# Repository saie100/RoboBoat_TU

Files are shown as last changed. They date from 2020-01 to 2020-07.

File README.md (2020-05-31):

# Temple University RoboBoat - Senior Design 2020 #



## Table of Contents ##

1. ### [ROS Packages & Implementation](/ROS_Packages#ros-packages) ###
    1. [Status Indicator Light & Autonomous Mode Select](ROS_Packages/roboboat_control_status)
    1. [Rosserial - multiple serial nodes](ROS_Packages/roboboat_rosserial)
    
1. ### [Arduino Code](Arduino_Files/) ###
    
1. ### [Shell Scripts](Shell_Scripts/) ### 
    1. [General Use of the Shell Scripts](/Shell_Scripts#general-use-of-the-shell-scripts)
    1. [Starting and stopping the boat's software](/Shell_Scripts#starting-and-stopping-the-boats-software)
    1. [Starting and stopping the boat's software for debugging](/Shell_Scripts#starting-and-stopping-the-boats-software-for-debugging)
    1. [Creating rosbag recordings](/Shell_Scripts#creating-rosbag-recordings)

1. ### [The Boat's Control Interface (Website)](Boat_Website/) ### 
    1. [HTML Code](Boat_Website/index.html)
    1. [Javascript Code](Boat_Website/src/)
    1. [CSS Styling](Boat_Website/main.css)
    
1. ### [The Computer Hardware](Computer_Hardware/) ### 

1. ### [Networking](Networking/) ###
    1. [IP Addresses for the Networking Devices](Networking#network-hardware-ips)
    1. [Reserved Device IP Addresses](Networking/README.md#reserved-device-ips)
    1. [Modifying the WDS Bridge](Networking/Modifying_WiFi_Bridge.md)
    1. [Backup & Restore the Network Equipment](Networking/RouterBackups/)
    1. [Connecting the Boat to the Internet](Networking/Connect_to_Internet.md)
    1. [Documentation from the Manufacturers](Networking/README.md#hardware-documentation)

1. ### [KiCad Circuit Schematics](KiCad_Schematics/) ###
    1. [Schematic PDF Files & Images](KiCad_Schematics/SchematicExports/)
    1. [Battery Monitoring System (KiCad Project)](KiCad_Schematics/BatteryMonitor)
    1. [Emergency Transmitter/Receiver & Status Indicator Light (KiCad Project)](KiCad_Schematics/EmergencySystem)
    1. [Power Distribution & Protection (KiCad Project)](KiCad_Schematics/PowerDistribution)
    1. [Teensy3.2 for Motor Control, GPS, and IMU (KiCad Project)](KiCad_Schematics/TeensySchematic)

1. ### [CAD Designs](CAD_Files/) ###
    1. [Motor Mounts](CAD_Files/MotorMounts/)
    1. [Cable Cover](CAD_Files/CableCover/)
    1. [Teensy3.2 Enclosure](CAD_Files/TeensyEnclosure/)
    1. [LIDAR Enclosure](CAD_Files/LidarEnclosure/)
    1. [Other Parts](CAD_Files/Z-Other/)

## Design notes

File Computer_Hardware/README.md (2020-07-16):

# Computer Hardware #

## Configuration Guides ##

## [Raspberry Pi 4 Ubuntu Server - A Guide by James Chambers](https://jamesachambers.com/raspberry-pi-4-ubuntu-server-desktop-18-04-3-image-unofficial/) ##
This guide was used to install Ubuntu Server on the Raspberry Pi 4 so that ROS did not need to be compipled when installing.   

## [Develop on SSD - NVIDIA Jetson TX Dev Kits](https://youtu.be/ZpQgRdg8RmA) ##
The guide listed below was used to configure the TX2 to boot from an SSD. 

*Note: Only follow the guide up 4:57. Do not follow the steps after this time.*

## Creating/Restoring Backups Using a Linux Computer ##
### Creating a Backup ###
1. Connect the Micro SD card from the Raspberry Pi or the SSD from the TX2 to the computer where the backup will be made. 
1. Unmount the Micro SD card or the SSD from the OS - this can be done in the disk manager. 
1. Use the following command after substituting the path to the Micro SD card or the SSD and specifing a name for the compressed backup of the drive.
```
	sudo dd if=/dev/r[INSERT_DISK_HERE(disk2)] BS=32m | gzip > /[INSERT_PATH_AND_BACKUP_NAME_HERE].gz
```
### Restoring a Backup ###
1. To write the backup to a Micro SD card or SSD, first connect the drive to the computer and unmount the disk. 
1. Use the following command after substituting the name of the drive to be written to and the name of the backup file.  
```
	gzip -dc /[INSERT_PATH_AND_BACKUP_NAME_HERE].gz | sudo dd of=/dev/r[INSERT_DISK_HERE(disk3)] BS=32m
```

## [DOWNLOAD: Raspberry Pi 4B - Ubuntu Server Backup](https://drive.google.com/uc?export=download&confirm=n3Q3&id=1xh1nTMyLx9h_HU1v4K-zJbxssuq-ram7) ##
*Note: This backup must be restored to a Micro SD Card with a capacity greater than or equal to 64GB*

## [DOWNLOAD: Jetson TX2 - NVIDIA Jetpack Backup](https://drive.google.com/uc?id=1ChVVHlB_Lbe0hwe4Fh0JUX25fiE8jmSy&export=download) ##
*Note: This backup must be restored to an SSD with a capacity greater than or equal to 500GB*

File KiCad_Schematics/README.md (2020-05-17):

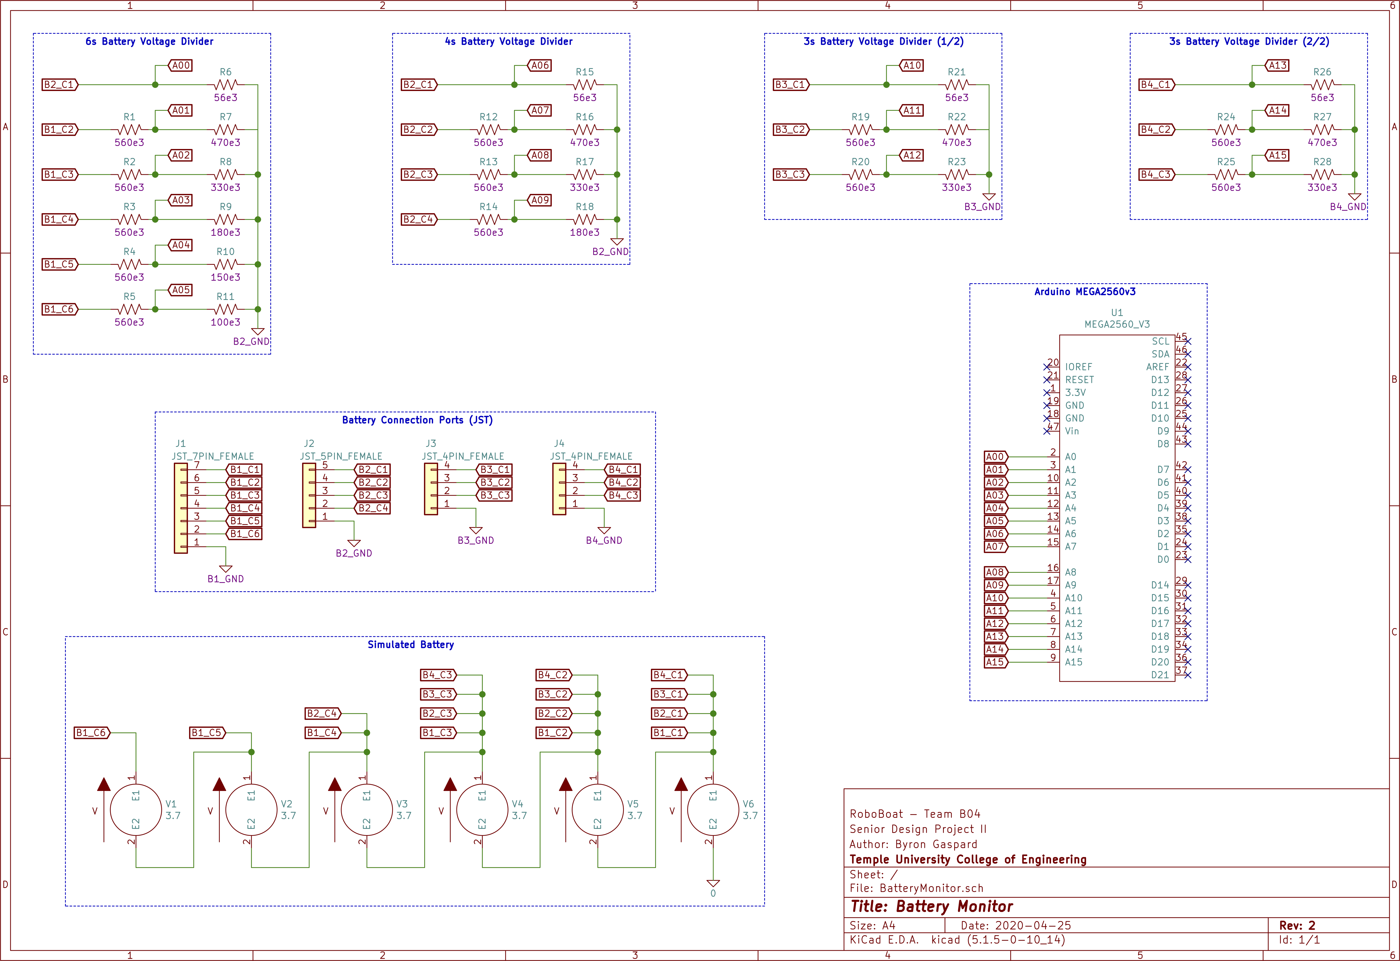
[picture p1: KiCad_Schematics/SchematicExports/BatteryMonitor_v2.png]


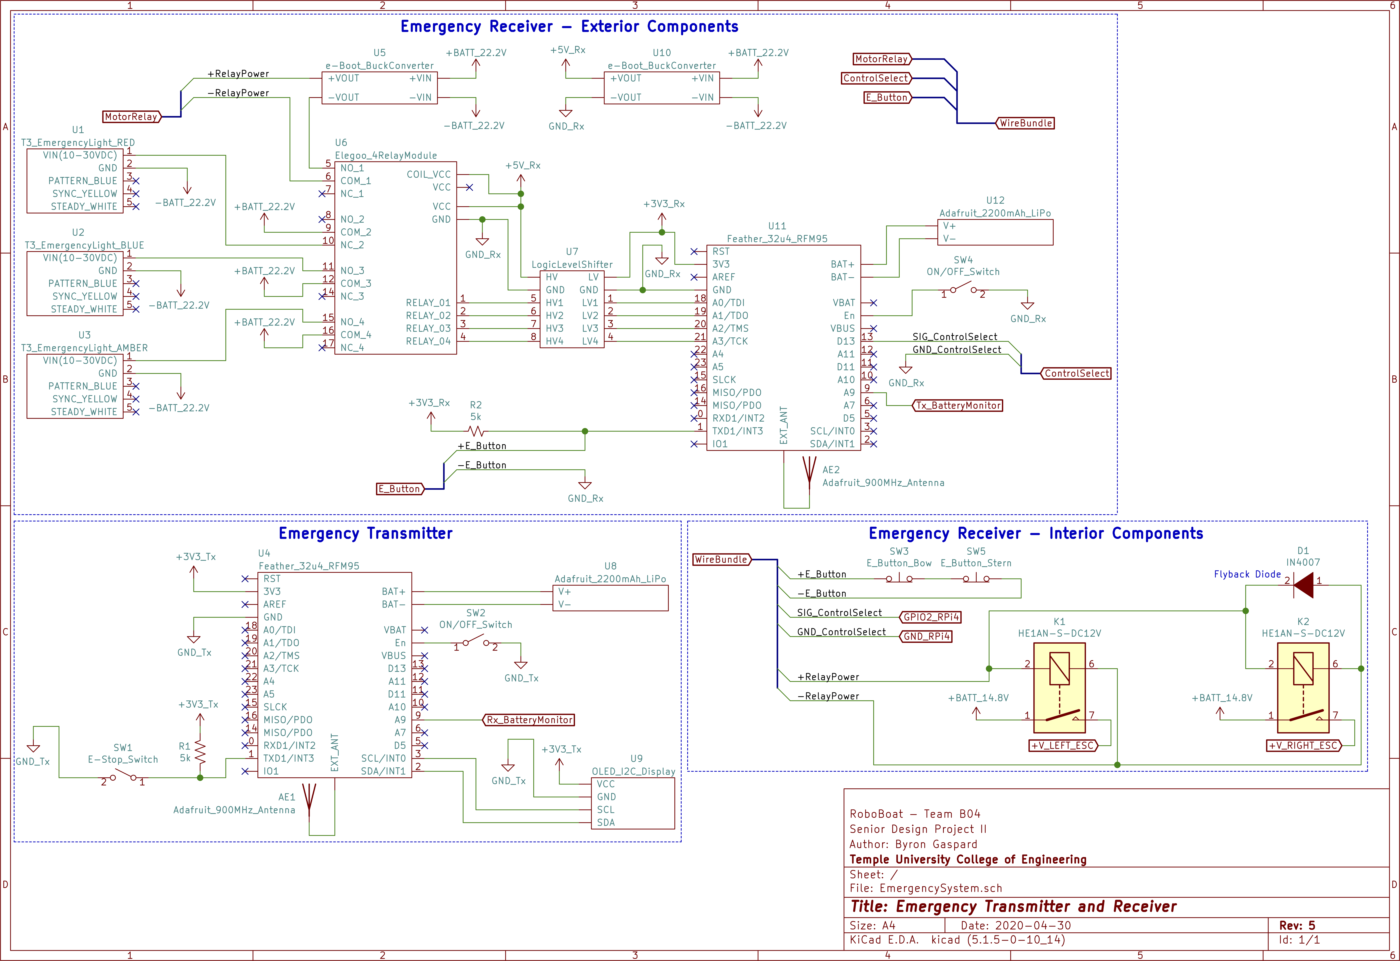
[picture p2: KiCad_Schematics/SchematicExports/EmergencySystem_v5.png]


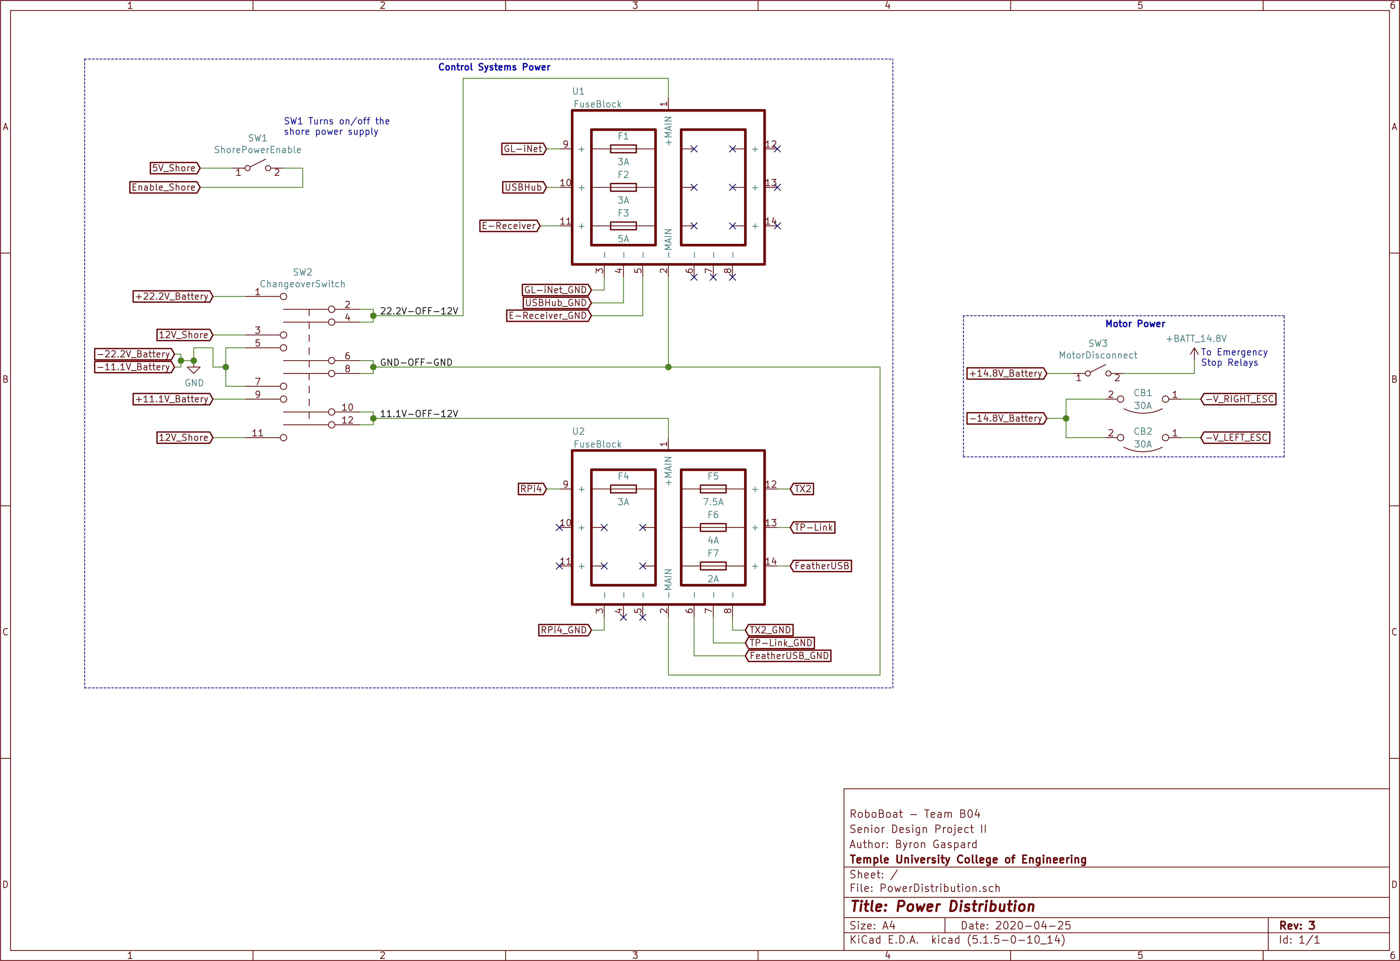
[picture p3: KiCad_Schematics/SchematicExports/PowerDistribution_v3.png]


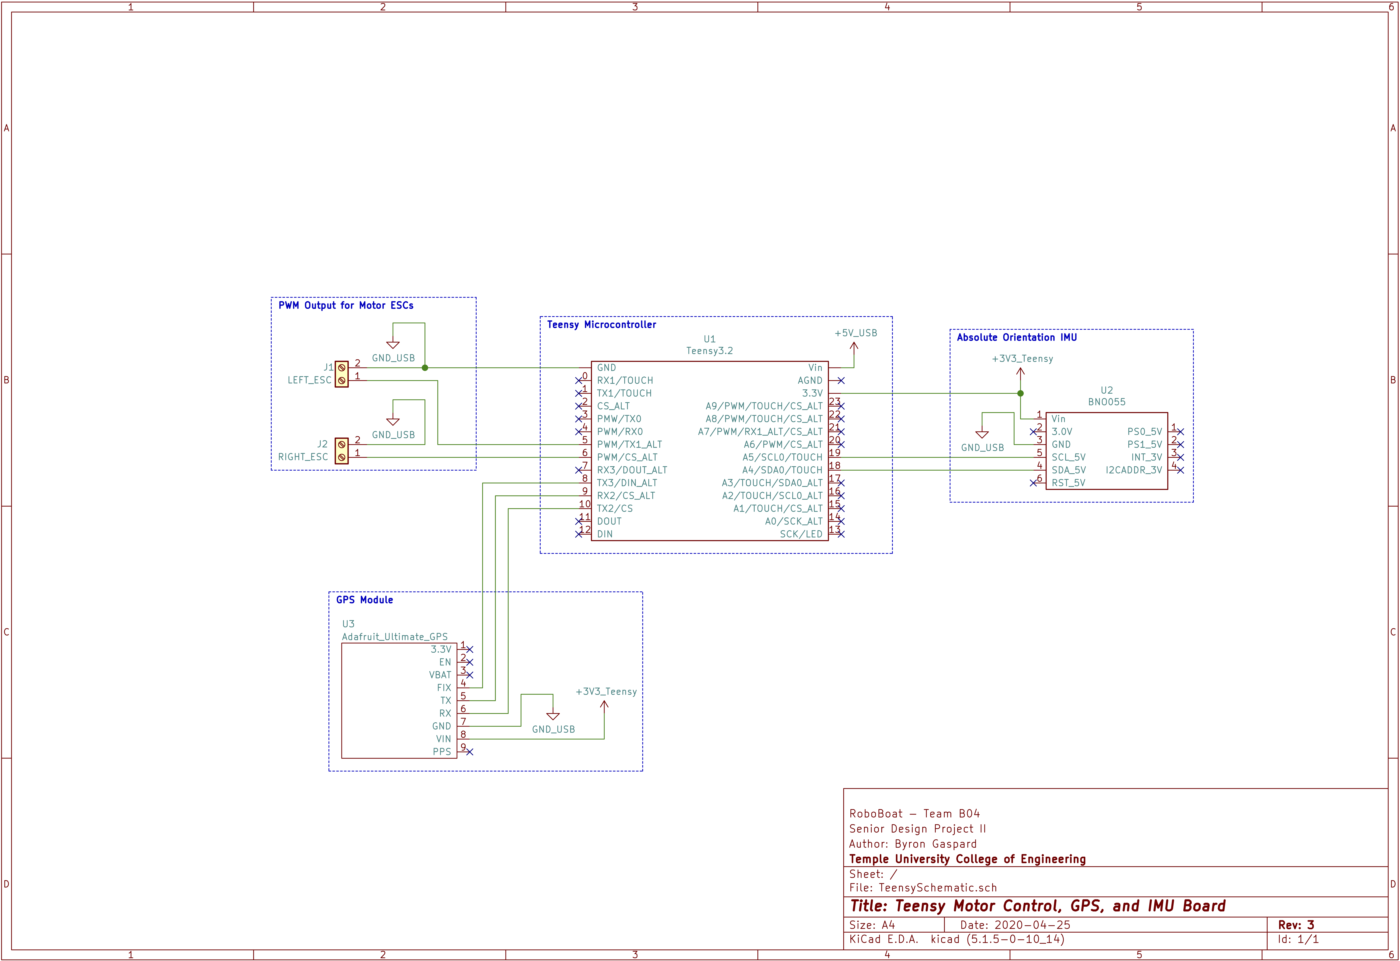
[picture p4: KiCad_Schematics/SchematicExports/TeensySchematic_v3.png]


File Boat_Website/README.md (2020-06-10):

# Overview of the Boat's Control Interface #

## JavaScript Libraries ##
1. [roslibjs](http://wiki.ros.org/roslibjs) - Allows ROS to be accessed and interacted with from a browser.
1. [Chart.js](https://www.chartjs.org/) - Provides JavaScript charting for displaying sensor data.
1. [Mapbox GL JS](https://docs.mapbox.com/mapbox-gl-js/api/) - Provides JavaScript map generation for displaying GPS sensor data recorded on the boat.
1. [xeogl](https://xeogl.org/) - A WebGL 3D visualization engine with support for displaying and animating 3D models.

---
## Custom JavaScript Code ##
1. [ros_setup.js](src/ros_setup.js)
1. [ros_handlers.js](src/ros_handlers.js)
1. [gamepad_control](src/gamepad_control.js)
1. [chart_create.js](src/chart_create.js)
1. [chart_update.js](src/chart_update.js)
1. [OrientationAnimation.js](src/OrientationAnimation.js)

--- 
## Controlling the boat from the website ##
The image at the bottom of this page shows the final version of the boat's website. 

The [Logitech F310 Controller](https://www.logitechg.com/en-us/products/gamepads/f310-gamepad.html) is used to manually drive the boat.

Steps to activate manual control:
1. Connect the Logitech F310 to the computer that is on the boat's website
1. Press any button on the controller - this will "wake up" the website and let it know that a controller is connected
1. Without pressing either of the joysticks, press the the "**Start**" button on the controller to zero the controller axis. 
1. The left and right motors on the boat can now be controlled independently using the left and right joystics on the F310. The axis can be re-zeroed at any point by pressing the "**Start**" button on the controller again.  



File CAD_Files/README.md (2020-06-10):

---

<p align="center">
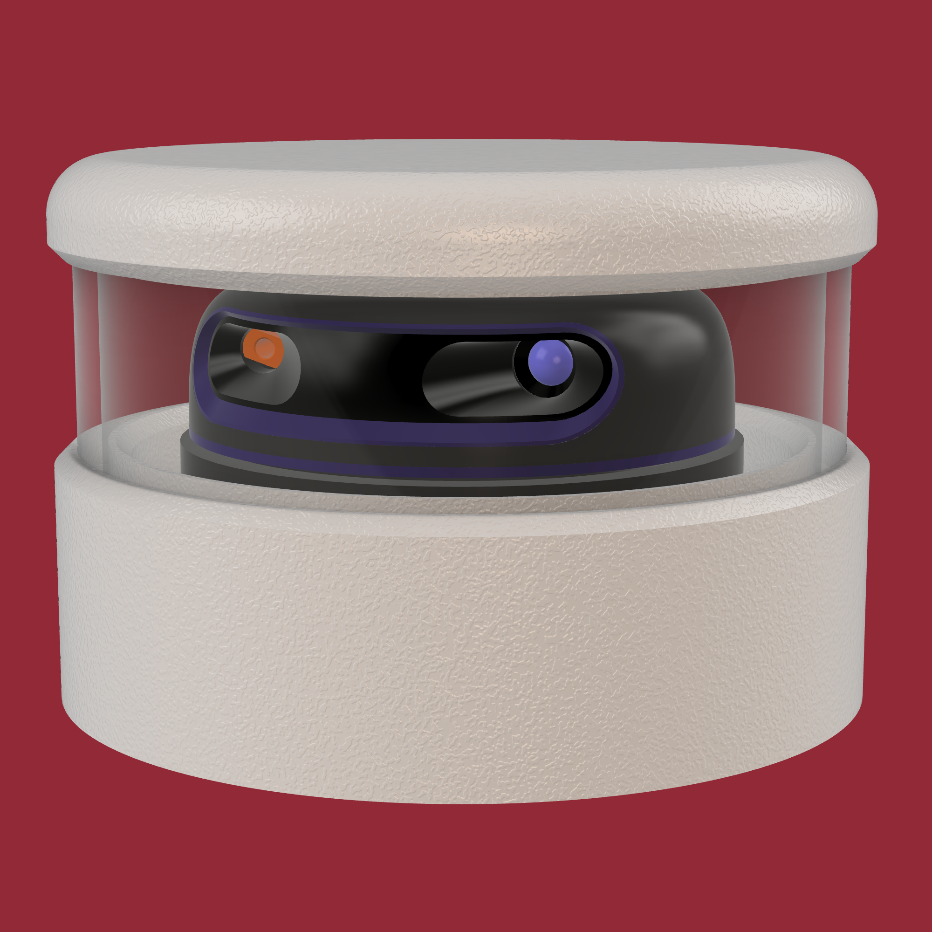
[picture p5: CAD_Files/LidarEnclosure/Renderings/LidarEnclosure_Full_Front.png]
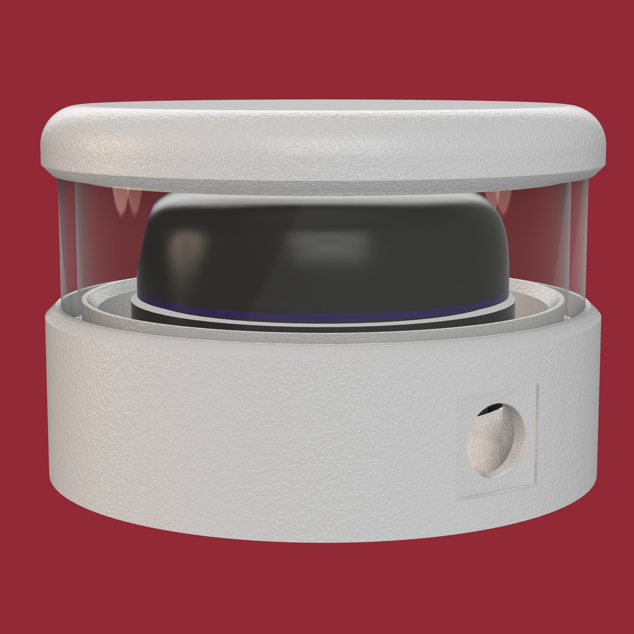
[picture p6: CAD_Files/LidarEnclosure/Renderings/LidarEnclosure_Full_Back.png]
   
</p>

---

<p align="center">
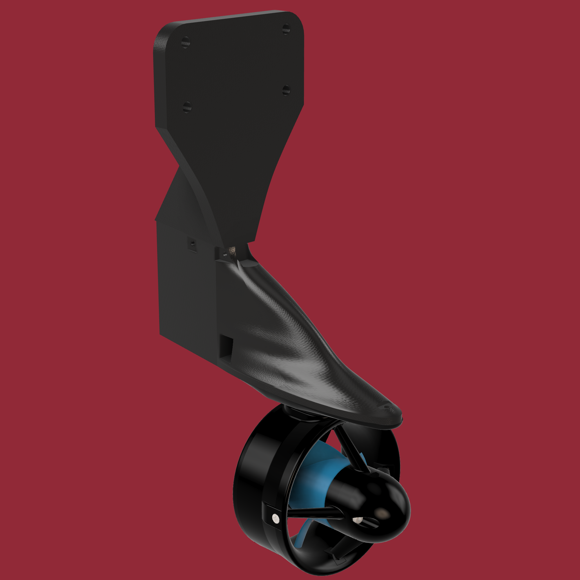
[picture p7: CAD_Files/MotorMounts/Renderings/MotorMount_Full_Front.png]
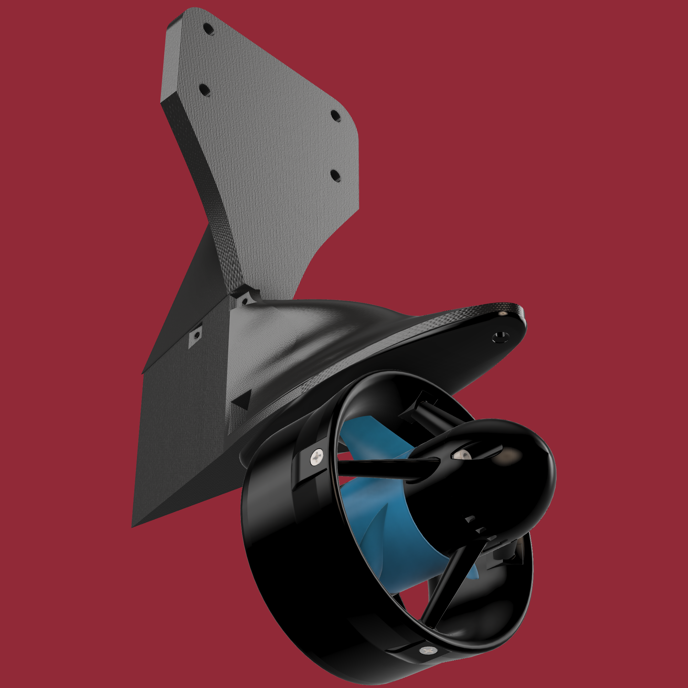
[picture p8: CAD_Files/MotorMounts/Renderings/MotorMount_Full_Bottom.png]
   
</p>

---

<p align="center">
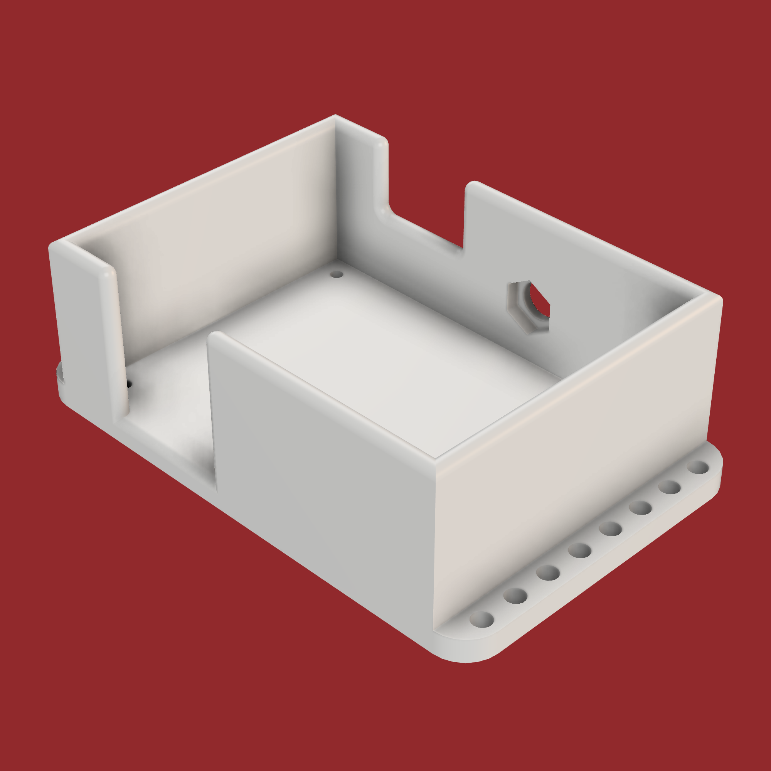
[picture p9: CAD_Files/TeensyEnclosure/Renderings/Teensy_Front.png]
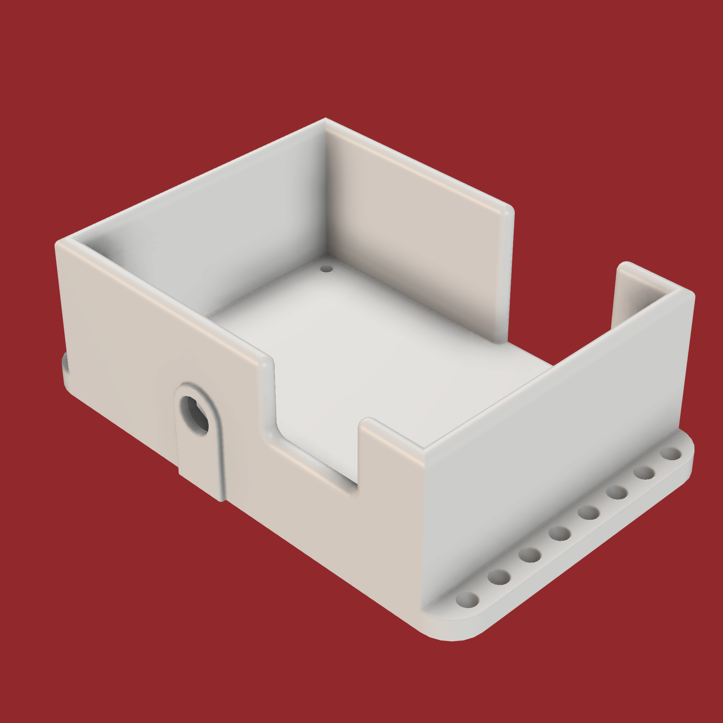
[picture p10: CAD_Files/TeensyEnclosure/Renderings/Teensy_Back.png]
   
</p>

---

<p align="center">
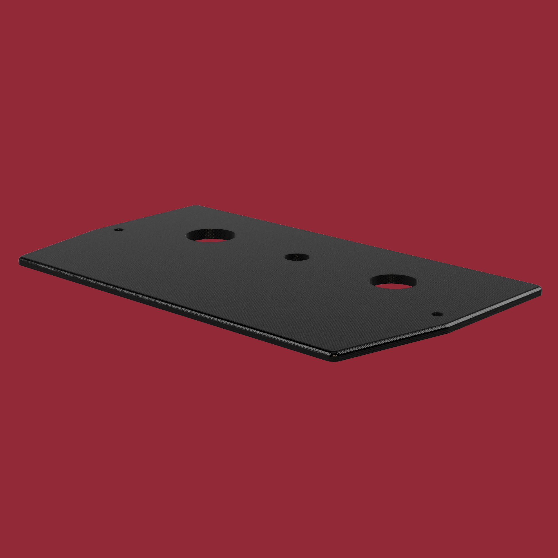
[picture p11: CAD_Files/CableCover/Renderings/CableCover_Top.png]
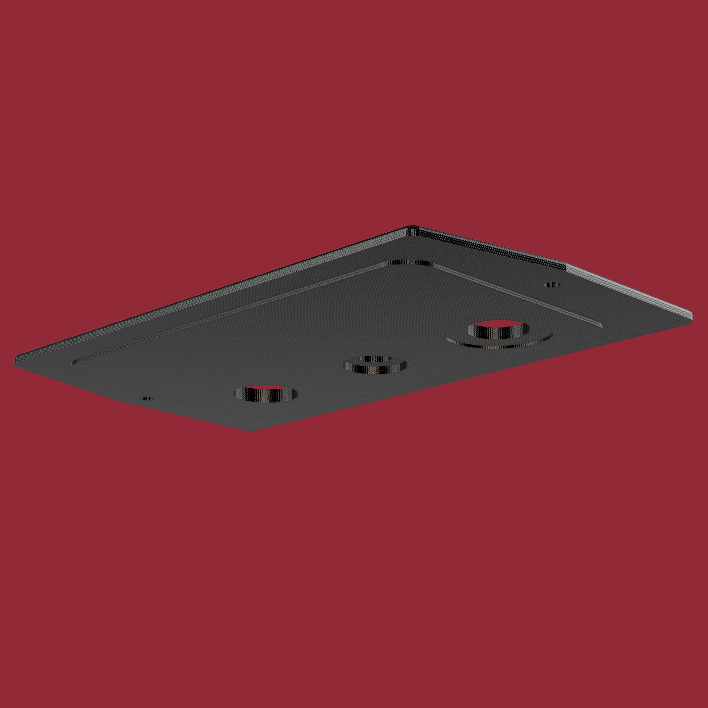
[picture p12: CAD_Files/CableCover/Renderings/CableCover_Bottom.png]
   
</p>

test

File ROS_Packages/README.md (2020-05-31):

# ROS Packages #
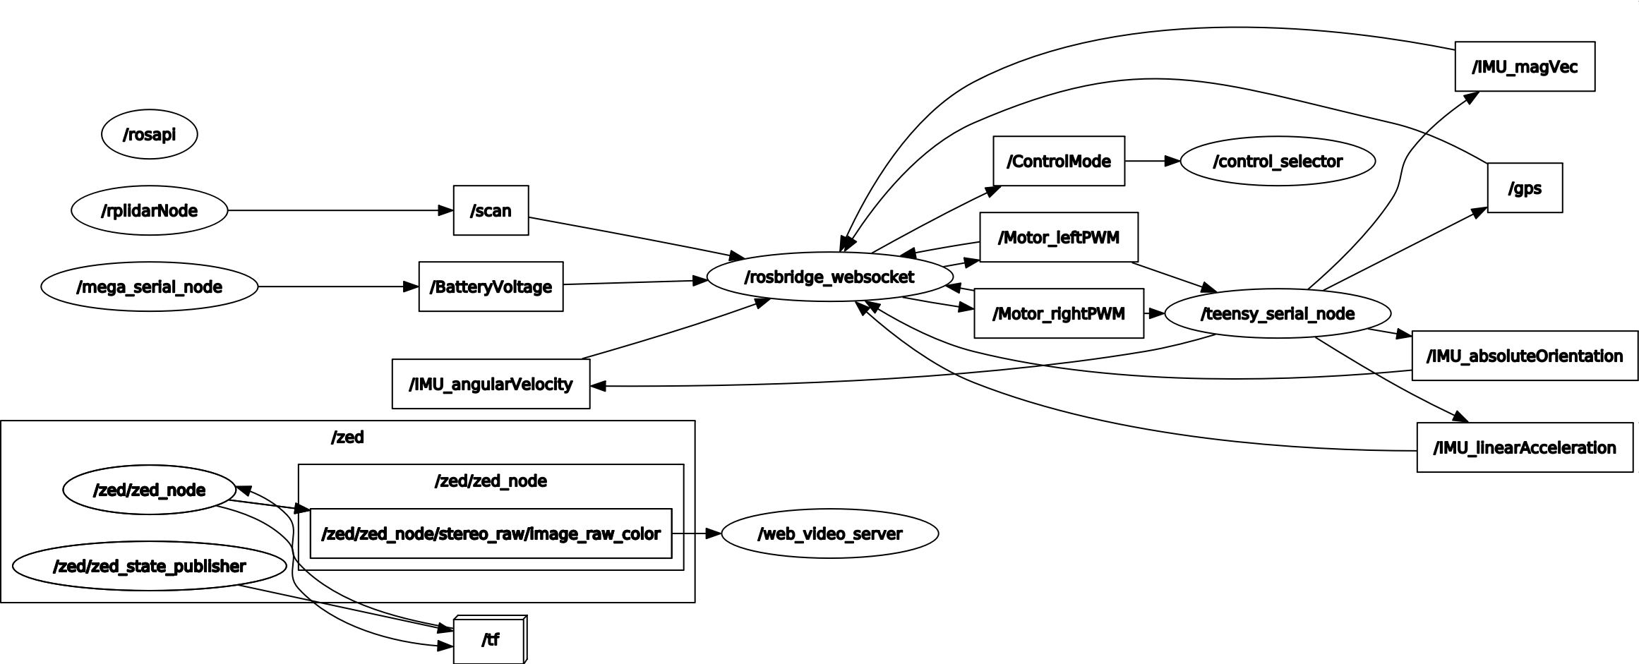
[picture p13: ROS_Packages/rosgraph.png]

## ROS Packages In Use ##
1. [zed-ros-wrapper](http://wiki.ros.org/zed-ros-wrapper) - Used to interface with the ZED stereo camera through ROS
1. [rplidar](http://wiki.ros.org/rplidar) - Used to interface with the RPLIDAR A3 through ROS
1. [rosserial](http://wiki.ros.org/rosserial) - Used to interface with the Teensy3.2 (for IMU, GPS, and motor control) and the Arduino MEGA2560 (for battery monitoring) through ROS
1. [rosserial_arduino](http://wiki.ros.org/rosserial_arduino) - Used to create the Arduino libraries on the Teensy3.2 an Arduino MEGA2560 for interfacing with the ROS network
1. [rospy](http://wiki.ros.org/rospy) - Used to create the ROS Python node for controlling the status indicator lights and starting/stopping autonomous routines
1. [rosbridge_suite](http://wiki.ros.org/rosbridge_suite) - Used to create a web interface for the ROS network for controlling and monitoring the boat
1. [web_video_server](http://wiki.ros.org/web_video_server) - Used to stream the camera feed from the ZED stereo camera to the website directly from the TX2

## Custom ROS Packages ##
1. [roboboat_control_status](roboboat_control_status/) - A ROS Python node that subscribes to the */ControlMode* topic to update the status light and to start/stop autonomous routines. The */ControlMode* message is an integer that corresponds to a specific operational mode. A message of 0 indicates manual control mode. A message of any other value indicates a specific autonomous routine. The status light mode is controlled with a GPIO pin and the [RPi.GPIO](https://pypi.org/project/RPi.GPIO/) library is used to control the RPi 4's GPIO signal for this purpose.
1. [roboboat_rosserial](roboboat_rosserial/) - The generic *rosserial* Python script provided in the package was modified to create two new python scripts. This was done as the ROS network has two *rosserial* nodes and using the default *rosserial* Python script would have resulted in errors as two nodes with the same name would be created. The names of *teensy_serial_node* and *mega_serial_node* were used in the two new python scripts and the serial ports that these devices are connected to were also checked/updated in the python script.

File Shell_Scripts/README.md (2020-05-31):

# General Use of the Shell Scripts #

All of the boat's core tasks are started & stopped from the RPi 4. The ROS master node is run on the RPi 4. ROS nodes are launched on the TX2 through commands sent over SSH.

SSH keys are generated that allow the RPi 4 to send commands to the TX2 over SSH without having to enter a password for each command sent. See [this guide](https://www.linuxbabe.com/linux-server/setup-passwordless-ssh-login) for instructions on how to generate an SSH key pair for password-less ssh.

---
## Starting and stopping the boat's software ##
1. Supply power to the boat (battery or wall power). The RPi 4 will turn on automatically when power is supplied, but the power button on the TX2 needs to be pressed to turn it on.
1. Connect power to the emergency system and turn on the Emergency Receiver by switching the two switches on the wire harness that connects the bottom of the boat to the top of the boat to the on position.
1. SSH into *ubuntu* account the RPi 4 at 10.19.122.101
    ```
    ssh ubuntu@10.19.122.101
    ```
1. Once logged in, navigate to this directory on the RPi 4
    ```
    cd RoboBoat_TU/Shell_Scripts/
    ```
1. Start the boat using the `noGUI` version of the starting shell script
    ```
    ./Startboat-noGUI.sh
    ```
1. After the boat is started, it can be stopped by pressing the **Enter** key when in the terminal window. It is important to stop the boat this and NOT to simply terminate the shell script process (**Ctrl+C**) as this will not stop the LIDAR's motor.

---
## Starting and stopping the boat's software for debugging ##
1. Login to the RPi 4's XRDP session at 10.19.122.101 using the Microsoft Remote Desktop ([Windows](https://www.microsoft.com/en-us/p/microsoft-remote-desktop/9wzdncrfj3ps?activetab=pivot:overviewtab)/[Mac](https://apps.apple.com/us/app/microsoft-remote-desktop/id1295203466?mt=12))
1. Once logged in, navigate to this directory on the RPi 4
    ```
    cd RoboBoat_TU/Shell_Scripts/
    ```
    
1. Start the boat using the `GUI` version of the starting shell script. A new terminal window will be created with tabs corresponding to each of the processes that were started on the boat that can be monitored while debugging.
    ```
    ./Startboat-GUI.sh
    ```
    
1. After the boat is started, it can be stopped using another shell script
    ```
    ./killboat.sh
    ```

---
## Creating rosbag recordings ##
1. Over SSH
    1. After the boat is started, open a new terminal window or a new SSH session on the RPi 4.
        ```
        ssh ubuntu@10.19.122.101
        ```
    1. Navigate to this directory on the RPi 4
        ```
        cd RoboBoat_TU/Shell_Scripts/
        ```
    1. Start recording a new rosbag file that will be saved in the `~/rosbag_files` directory on the TX2.
        ```
        ./start-rosbag.sh
        ```
    1. To stop the recording, terminate the process by pressing **Ctrl+C**. Always remember to stop the rosbag recording before stopping the ROS system.
1. In the GUI
    1. Open a new terminal window or tab
    1. Navigate to this directory on the RPi 4
        ```
        cd RoboBoat_TU/Shell_Scripts/
        ```
    1. Start recording a new rosbag file that will be saved in the `~/rosbag_files` directory on the TX2.
        ```
        ./start-rosbag.sh
        ```
    1. To stop the recording, terminate the process by pressing **Ctrl+C**. Always remember to stop the rosbag recording before stopping the ROS system.

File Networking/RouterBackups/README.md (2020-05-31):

# How to Backup & Restore the Boat's Network Equipment #
---
## TP-Link AC1750 ##
1. Select the "**Advanced**" tab at the top of the router management portal (located at [10.19.122.1](http://10.19.122.1) if the router was configured using the files in this directory, or [192.168.0.1](http://192.168.0.1) if the router has since been reset).
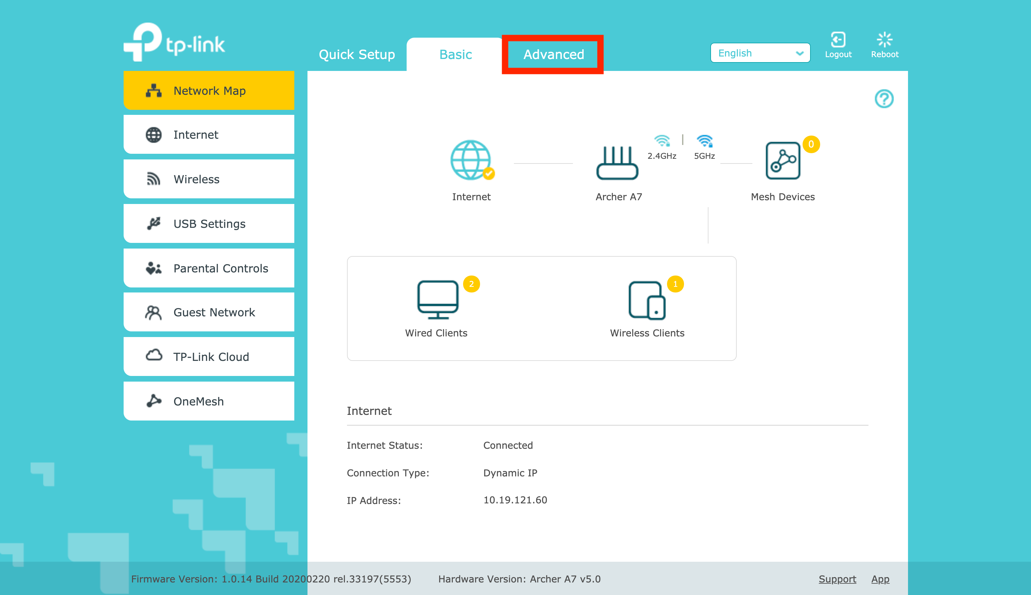
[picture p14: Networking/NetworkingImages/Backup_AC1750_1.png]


1. Select the "**System Tools**" option from page categories listed on the left of the management portal.
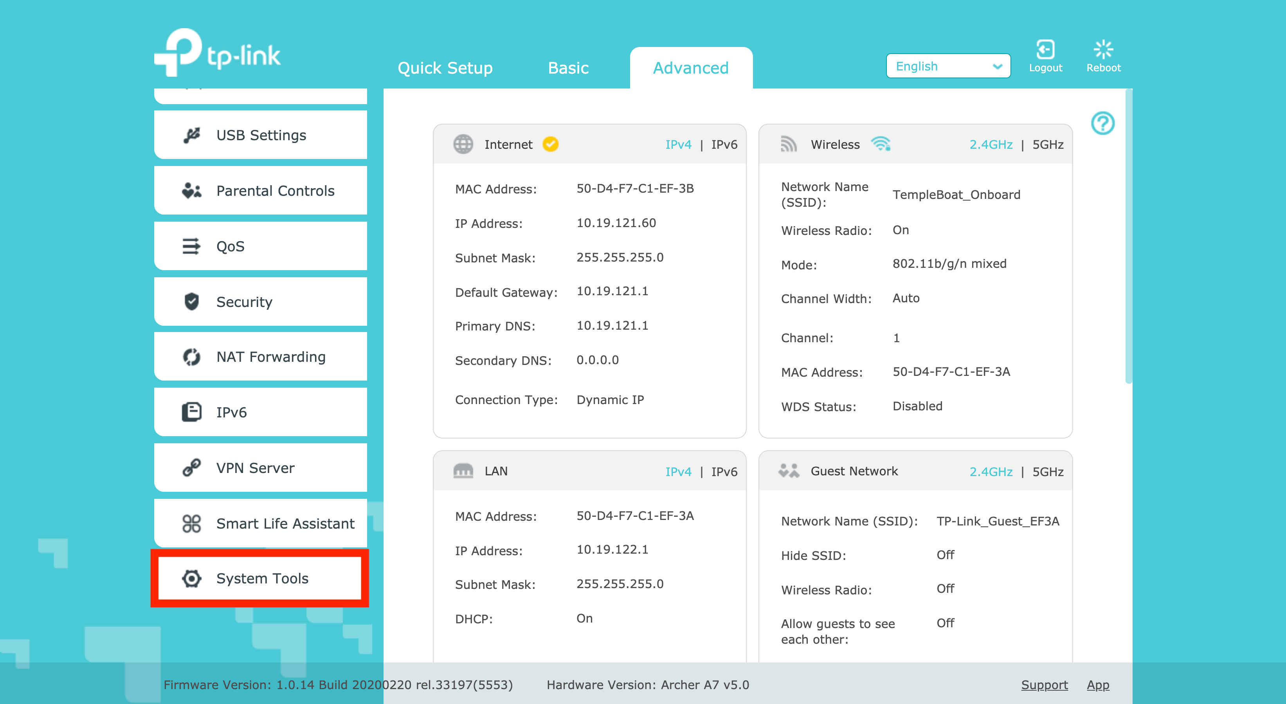
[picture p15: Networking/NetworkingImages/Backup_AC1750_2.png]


1. Select the "**Backup & Restore**" page from the drop-down menu that appeared after clicking "**System Tools**" in step 2.
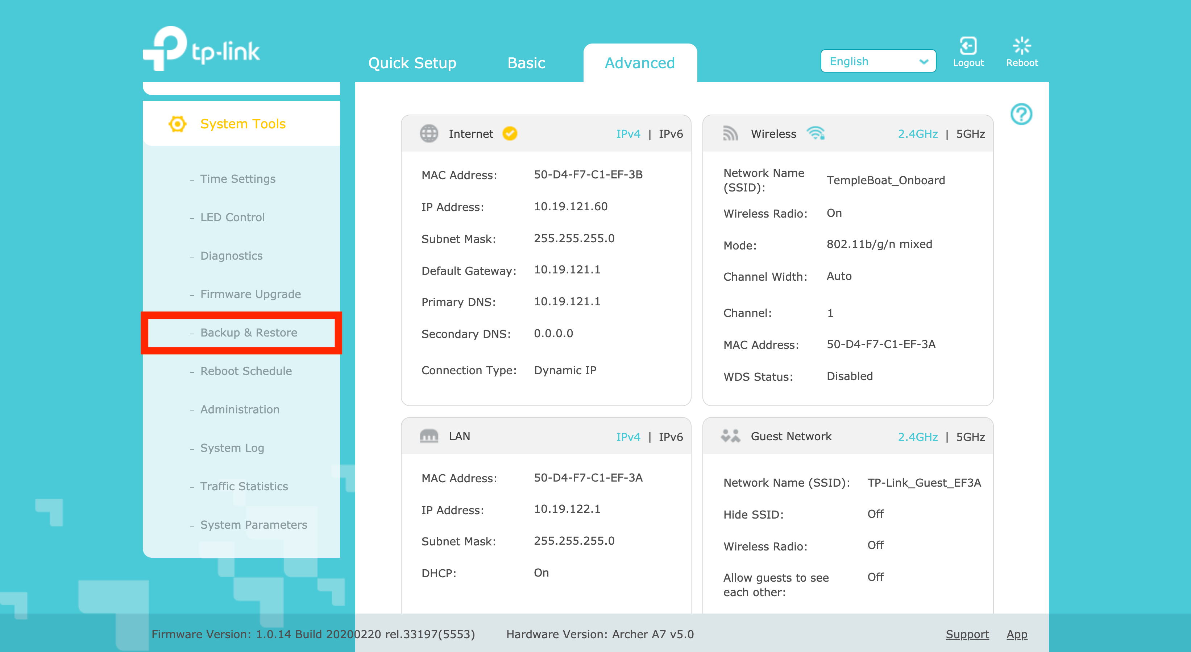
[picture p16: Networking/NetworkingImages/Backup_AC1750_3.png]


1. Here you can either (i) backup the current configuration, or (ii) restore to a previously backed-up configuration.
  1. Click the "**Backup**" button to generate a new backup that you are able to save on your local machine.
  1. Under the "**Restore**" section of the page, click the "**Browse**" button and locate the previously generated backup file on your local machine. Next, click the "**Restore**" button to complete the router restore process.

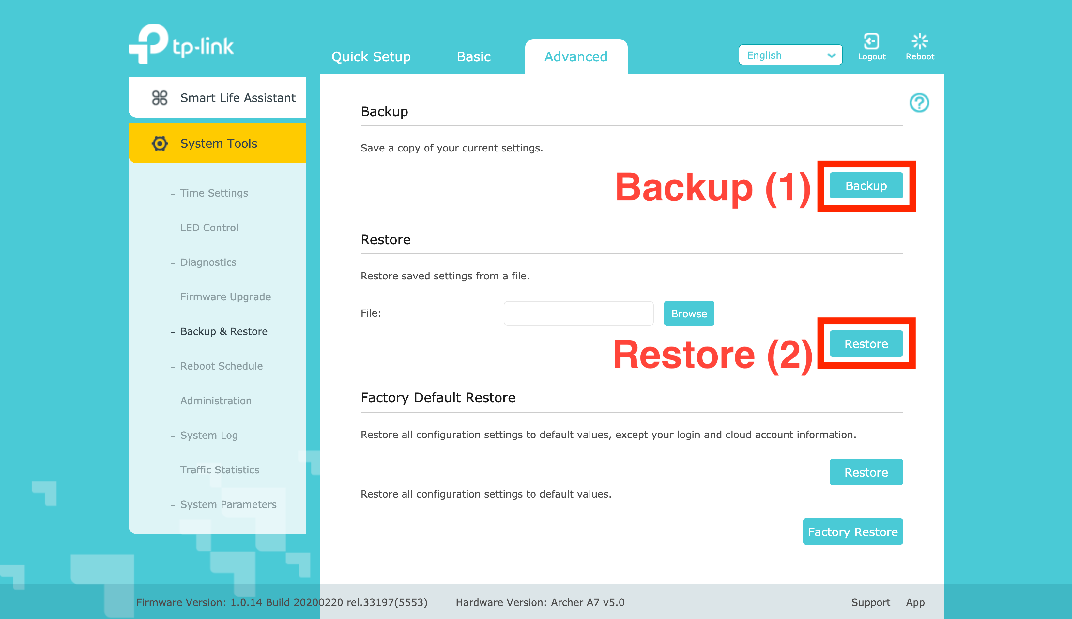
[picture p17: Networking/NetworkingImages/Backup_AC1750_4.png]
  

---
## TP-Link AC1200 ##

***NOTE: If this router is configured with the WDS and has its DHCP server disabled, you will not be able to directly access the management console by connecting to the network. Instead you will have to edit your computer's network settings. See [Modifying_Wifi_Bridge.md](../Modifying_WiFi_Bridge.md#step-3-configuring-the-ac1200) for instructions on this procedure.***

1. Expand the "**System Tools**" menu in the router's management portal located at [10.19.123.1](http://10.19.123.1) if the router was configured using the files in this directory, or [192.168.0.1](http://192.168.0.1) if the router has since been reset.
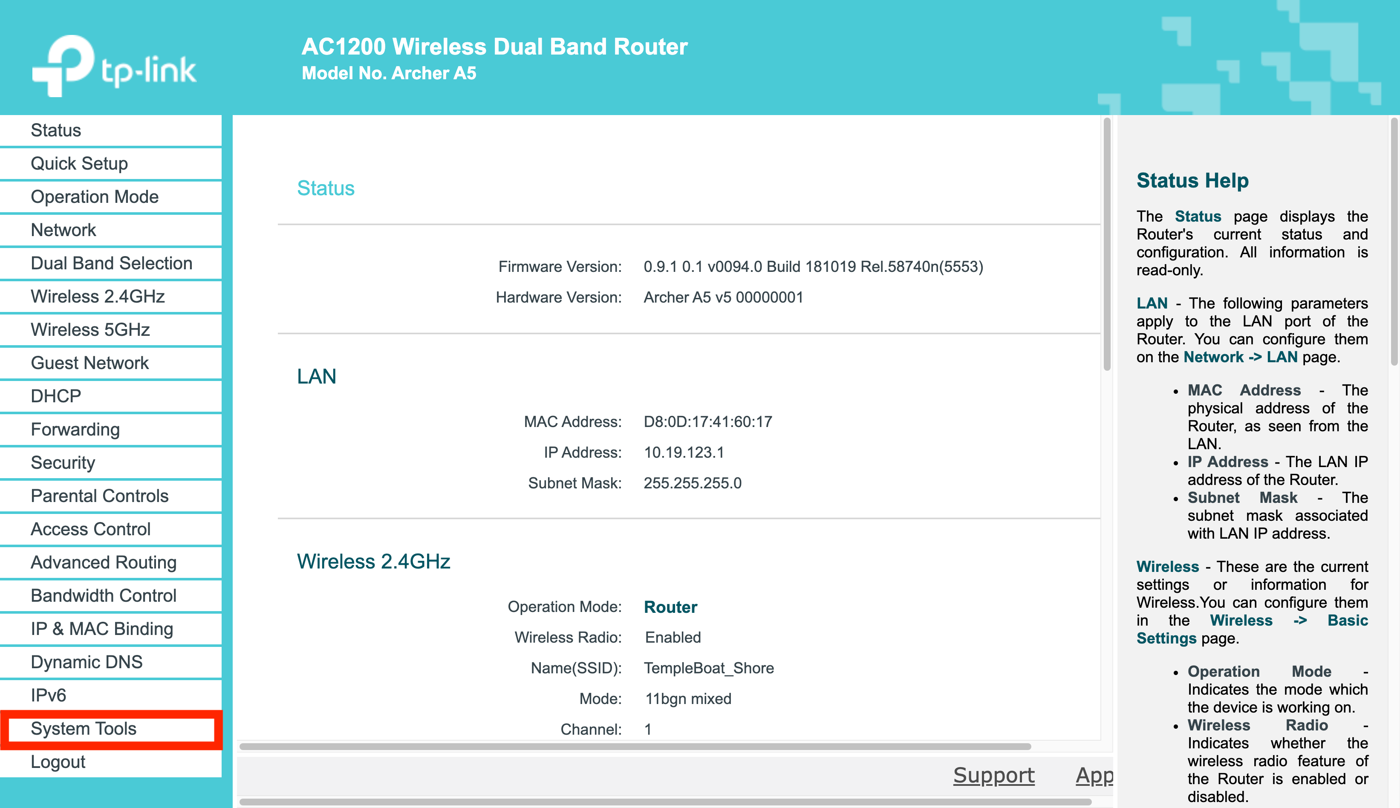
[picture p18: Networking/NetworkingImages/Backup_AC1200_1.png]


1. Select the "**Backup & Restore**" option from the expanded menu.
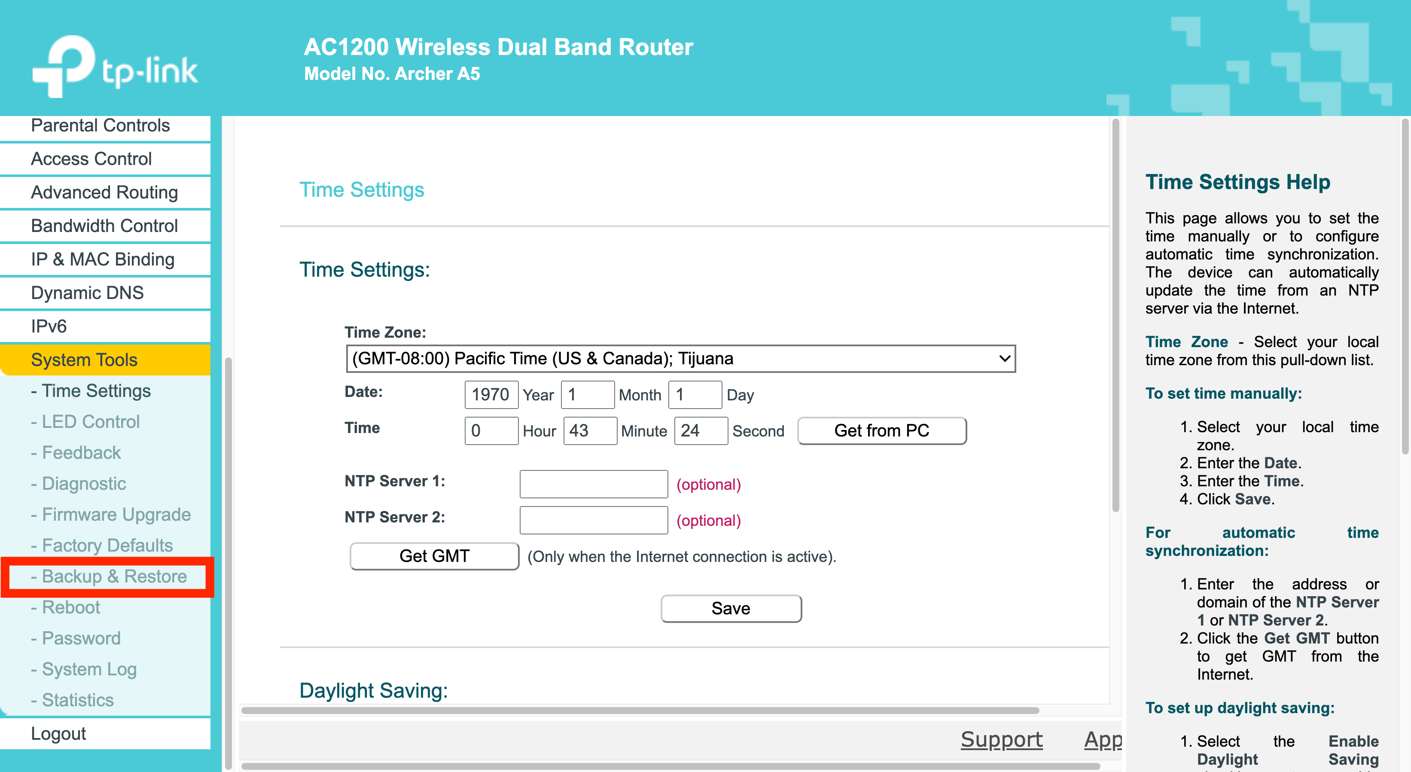
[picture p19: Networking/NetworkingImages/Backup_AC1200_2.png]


1.  Here you can either (i) backup the current configuration, or (ii) restore to a previously backed-up configuration.
  1. Click the "**Backup**" button to generate a new backup that you are able to save on your local machine.
  1.Click the "**Restore**" button and locate the previously generated backup file on your local machine. Next, click the "**Restore**" button to complete the router restore process.  

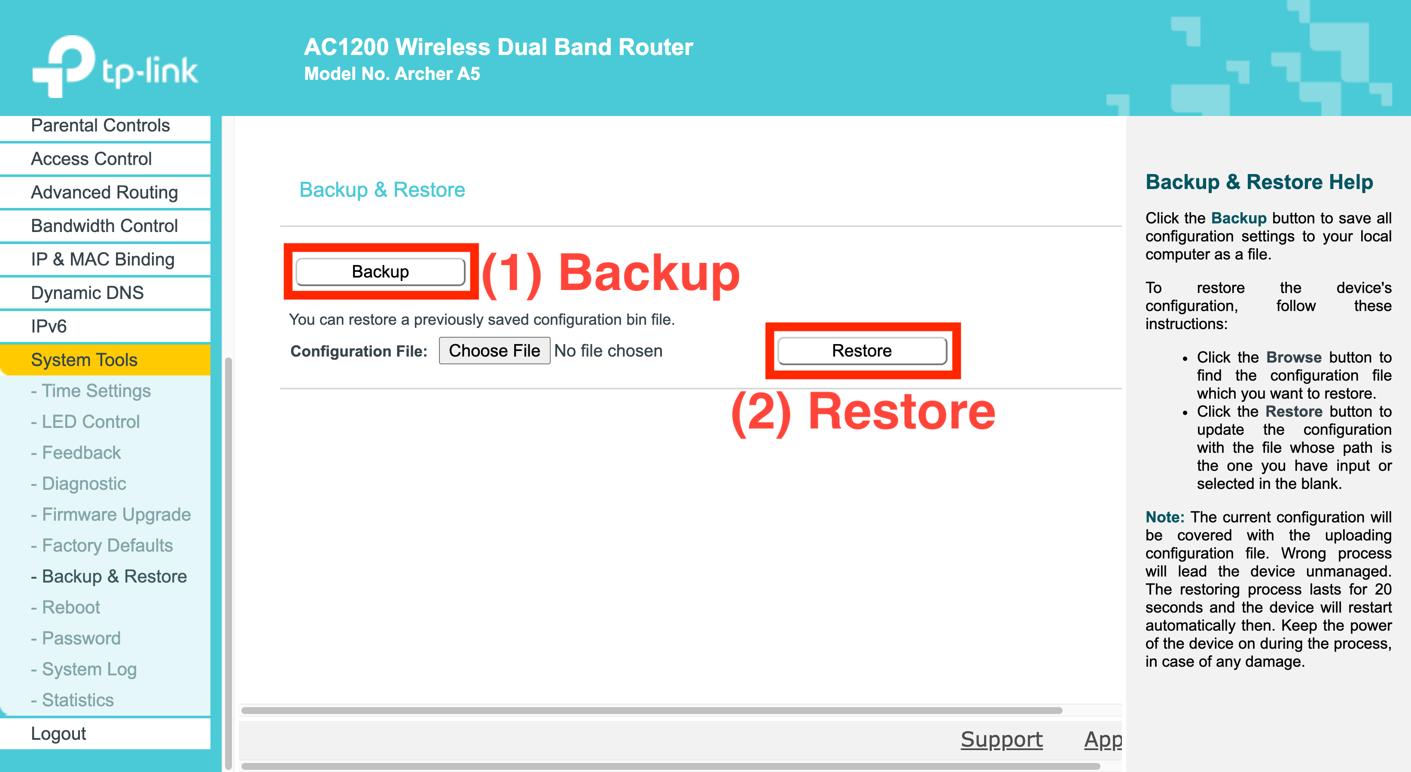
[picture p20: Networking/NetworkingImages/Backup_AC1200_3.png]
  

---
## GL.iNet GL-AR750 ##

1. Select the "**MORE SETTINGS**" drop-down menu on the left side of the router management portal (located at [10.19.121.1](http://10.19.121.1) if the router was configured using the files in this directory, or [192.168.8.1](http://192.168.8.1) if the router has since been reset).

1. Select "**Advanced**" from the drop-down menu.
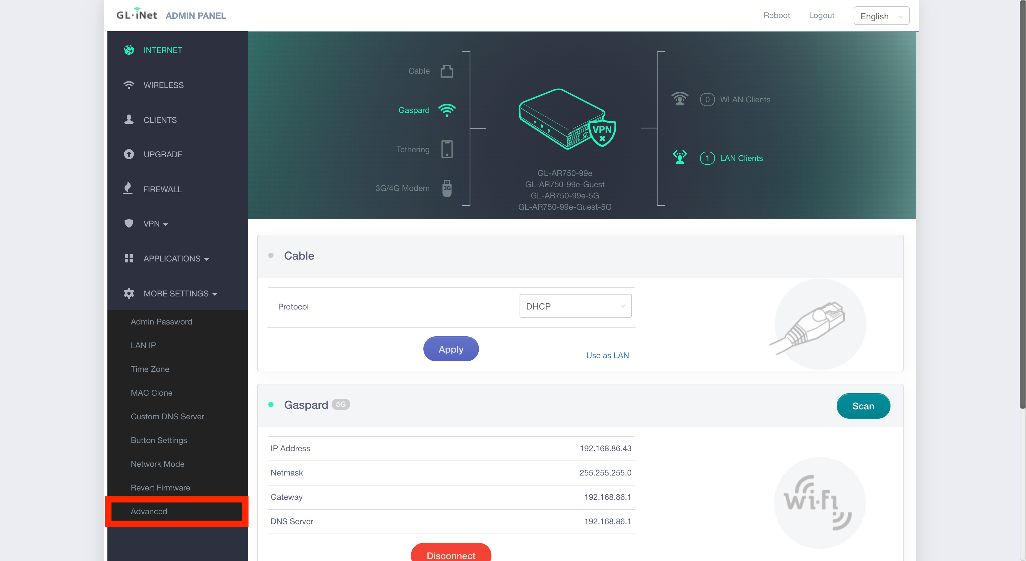
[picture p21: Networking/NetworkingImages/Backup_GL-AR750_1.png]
  

1. A new tab will open and present the login screen for the Open-WRT settings management portal. Login to the `root` account with the same password that you use to login to the router's main admin portal.
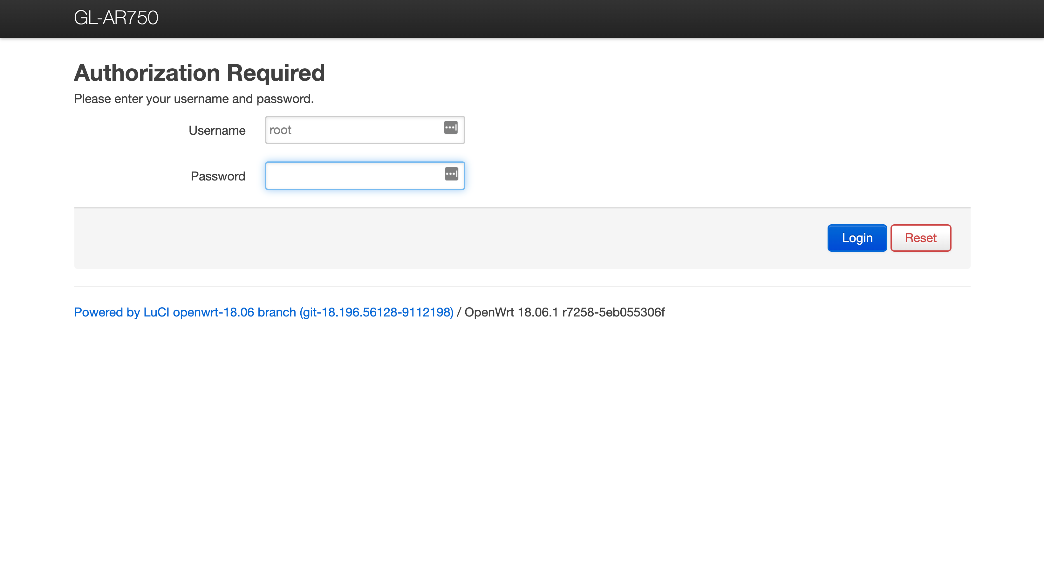
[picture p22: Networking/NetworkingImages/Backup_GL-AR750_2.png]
  

1. Hover over the "**System**" drop-down menu and click the "**Backup / Flash Firmware**" option from the list.
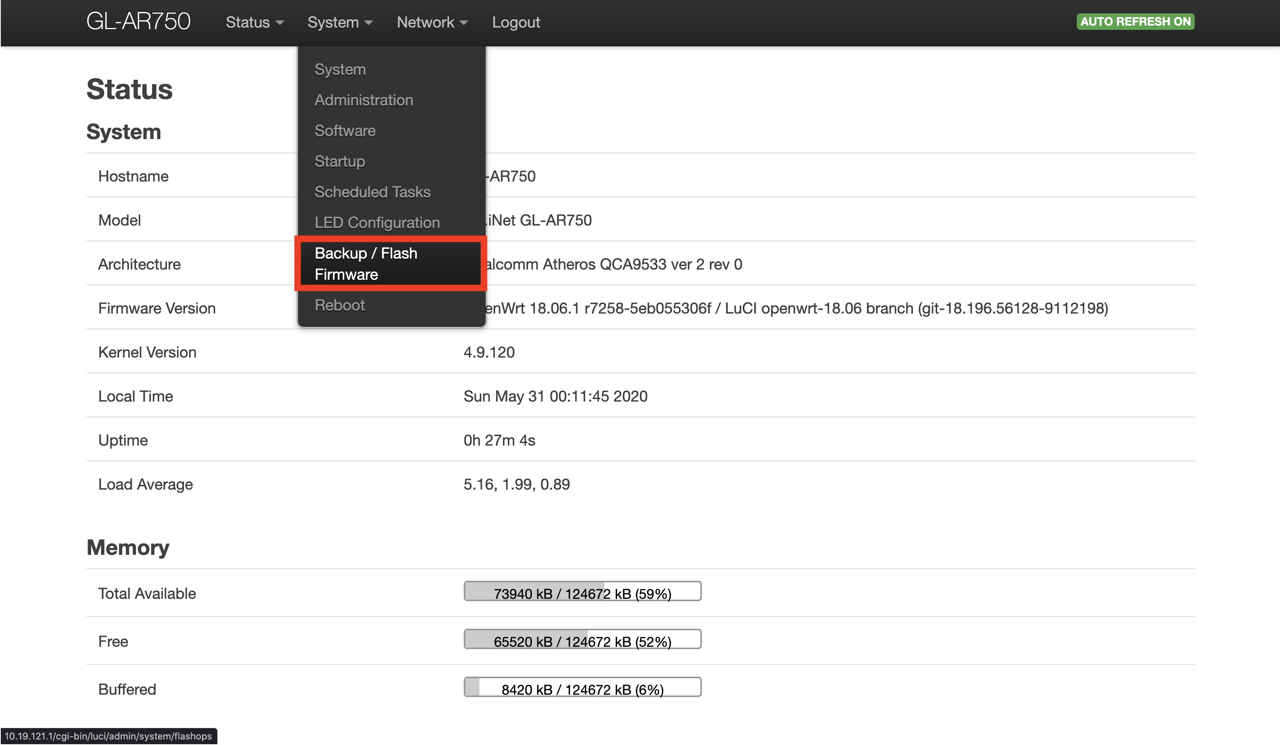
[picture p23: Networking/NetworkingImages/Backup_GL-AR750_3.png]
  

1. Here you can either (i) backup the current configuration, or (ii) restore to a previously backed-up configuration.
    1. Under the "**Backup**" section of the page, click the "**Generate archive**" button. A new backup will be made that you are able to save on your local machine.
    1. Under the "**Restore**" section of the page, click the "**Choose file**" button and upload the archive file that you wish to restore the router to. Next, click the "**Upload archive...**" button to complete the router restore process.

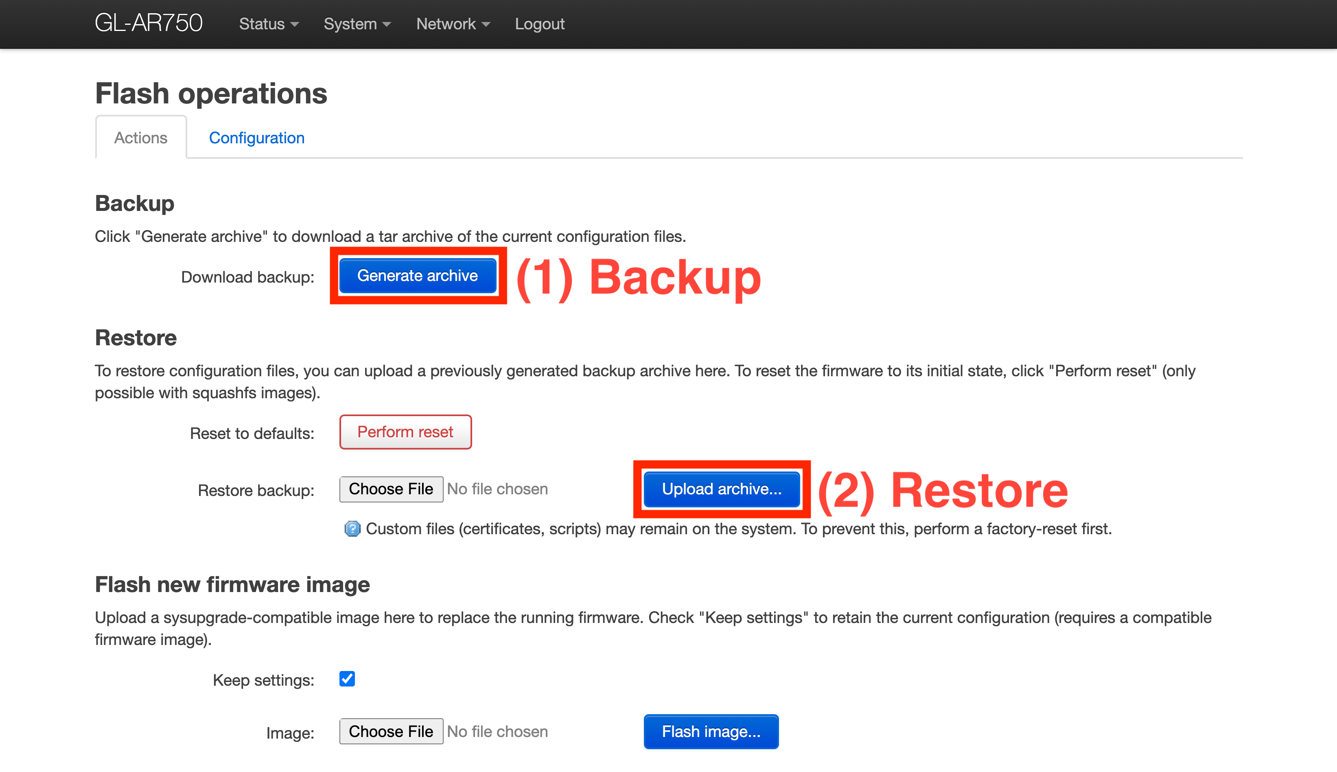
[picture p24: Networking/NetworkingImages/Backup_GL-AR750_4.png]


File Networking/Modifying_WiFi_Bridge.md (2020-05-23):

# Changing the channel and/or frequency of the bridged network #
---
## Background ##

The TP-Link AC1750 and AC1200 are bridged to form a WDS (Wireless Distribution System). In this configuration, the AC1750 installed on the boat handles the routing and runs the DHCP server while the AC1200 provides an alternative wired/wireless access point for connecting to the boat from the shore.

A bridged network is necessary as the RoboBoat competition rules require that all teams provide an RJ45 ethernet port on their shore-side control station to allow the competition staff to connect to an interface with the boat's computers.

When configuring a WDS, a wireless frequency band (2.4GHz or 5GHz) and a channel must be selected. Ideally, a frequency and channel with no or minimal usage should be selected to improve the connection quality by reducing interference. Different locations will likely have different wireless networks operating on different frequencies/channels. Therefore, it may be necessary to change the frequency and channel used to form the WDS to ensure the integrity of the communication link.

The WDS can be configured on either the 2.4GHz or 5GHz bands, but we recommend that the 2.4GHz band be used whenever possible as it provides a better transmission range.

---
## Step 1) Finding the optimal frequency/channel pair ##

 1. To find the optimal frequency and channel pair all routers with the exception of the GL.iNet GL-AR750 should be turned off.

 1. Next, a network utility such should be used to find the best frequency channel combination to create the WDS.
  - macOS: Using the **Wireless Diagnostics** stock macOS application.
     1. Open the **Wireless Diagnostics** app that is preinstalled
     1. From the menu options, select **Window**->**Scan**
     1. Click the **Scan Now** button in the bottom left corner of the window
     1. The summary table will contain the best channels for both the 2.4GHz and 5GHz frequencies, both of which are boxed in red below: 
  - Windows: Using the **WiFi Analyzer** application from the Microsoft Store
     1. Download the **WiFi Analyzer** application ([Download Link](https://www.microsoft.com/en-us/p/wifi-analyzer/9nblggh33n0n)).
     1. Open the application and click the **Analyze** icon at the top of the window
     1. The channel recommendation for the 2.4GHz band is shown at the bottom of the window and boxed in red in the example image below:
    
     1. The optimal 5GHz channel can be found by clicking on the **5 GHz** icon in the bottom right corner of the window shown above.

---
## Step 2) Configuring the AC1750 ##

Now that the optimal channel and band have been identified, the routers must be configured. First, we will configure the AC1750, which is installed on the boat.
 1. As the routers were turned off when finding the optimal channel/band, turn both routers (the AC1750 and AC1200) back on.

 1. Connect to the AC1750's network wirelessly (SSID: **TempleBoat_Onboard**) or with an ethernet cable

 1. Open a web browser and navigate to the AC1750's admin console (located at [10.19.122.1](10.19.122.1)).

 1. Login using the credentials and click on the the **Advanced** tab at the top of the web page, which is boxed in red in the screenshot below:
 

 1. Next, expand the **Wireless** menu (labeled as 1 in the image below) on the left side of the page and then select the **Wireless Settings** menu item (labeled as 2 in the image below).
 

 1. Finally, we need to configure the channel. Select the **Channel** drop-down list boxed in red in the image below and enter select the channel that the WDS will use on. If you are using the 5GHz band to form the WDS, click the **5GHz** text on the middle right of the page and enter the channel there.
 
  *Note: If you are creating a bridge on the 2.4GHz band, make sure that the Channel for the 5GHz band is set to "Auto", similarly, if you are bridging on the 5GHz band, make sure the Channel for the 2.4GHz band is set to "Auto".*

 1. After editing the **Channel** settings, make sure to click the **Save** button at the bottom of the page to complete the AC1750 configuration.

---
## Step 3) Configuring the AC1200 ##

The AC1200 is configured as an access point in the WDS for the AC1750's network, so the AC1200's DHCP server is disabled. Therefore, you cannot access the AC1200's admin console by connecting to the AC1200 opening its IP address in a web browser like we did for the AC1750. Instead, the computer being used to connect to the AC1200 must self-assign an IP address and select the the AC1200 as its router temporarily. If this is done correctly, we can then access the AC1200's management console to configure the WDS.

1. Connect to the AC1200's network wirelessly (SSID: **TempleBoat_Shore**) or with an ethernet cable.

1. Manually configure IPv4
  - macOS
    1. Open the **Network** settings in **System Preferences**
    

    1. Click the **Advanced...** button in the bottom right corner of the window
    

    1. In the **TCP/IP** tab, change the **Configure IPv4** drop-down menu from **Automatic** to **Manual** and then fill in the **IPv4 Address**, **Subnet Mask**, and **Router** text boxes with the information show below before clicking **OK**.
    

    1. Finally, click **Apply**. You should now be able to navigate to the AC1200's admin console in a web browser (located at [10.19.123.1](10.19.123.1)).
    

  - Windows
    1. After connecting to the AC1200, open the **Network & Internet** settings and then click on **Change connection properties** which is boxed in red in the image below:
    

    1. At the bottom of the new window, click the **Edit** button under the **IP assignment:** section, boxed in red below:
    

    1. Click the drop-down menu with the text **Automatic (DHCP)** (boxed in red below) and change it to **Manual**.
    

    1. Toggle the **IPv4** slider to **On** before filling in the fields as shown in the image below and then click **Save**. You should now be able to navigate to the AC1200's admin console in a web browser (located at [10.19.123.1](10.19.123.1)).
    

1. Navigate to the AC1200's admin console located at [10.19.123.1](10.19.123.1) and log in:


1. If bridging on the 2.4GHz band, click on the **Wireless 2.4GHz** menu (labeled as 1 in the image below) on the left side of the page. Next, select the **Channel** being used to create the WDS from the drop-down menu (labeled as 2 in the image below). Finally, click the **Scan** button to search for the AC1750's wireless network (labeled as 3 in the image below).


1. A new window will appear with the scan results and is shown in the image below. The AC1750's wireless network (**TempleBoat_Onboard**) can be seen on this list and is highlighted in red in the image below. Click the **Connect** link in the same row as AC1750's network (boxed in red in the image below) to select that network to form the WDS.


1. You will be returned to the **Wireless 2.4GHz** page after clicking **Connect** and the **SSID (to be bridged)** and **MAC Address (to be bridged)** fields will now be populated. Finally, enter the password for the AC1750's wireless network and click save.


1. Ensure that the DHCP server for the AC1200 is disabled by clicking the **DHCP** menu on the left of the admin console (labeled as 1 in the image below), selecting the **Disable** radio button next to the **DHCP Server:** label (labeled as 2 in the image below), and finally clicking **Save** (labeled as 3 in the image below).

 *Note: We want to disable the DHCP server on the AC1200 as we will only be using the AC1750's DHCP server.*

1. To validate that the WDS was correctly configured, click on the **Status** menu option on the left of the AC1200's admin console (labeled as 1 in the image below). Under the **Wireless 2.4GHz** section, the **WDS Status** should be **Connected** once the WDS is bridged (labeled as 2 in the image below). *Note: It may take several minutes for the WDS to bridge, so wait some time before troubleshooting if the bridge is not immediately established.*

  - If the WDS does not bridge, first double check that the password was entered correctly in the previous step.

---
## Step 4) Finalizing the setup ##

Lastly, the network settings on the computer used to connect to the AC1200 must be reverted back to the original state. The sim
- macOS
  1. Open the **Network** settings in **System Preferences**
  

  1. Click the **Advanced...** button in the bottom right corner of the window
  

  1. Under the **TCP/IP** tab, change the **Configure IPv4:** drop-down selection to **Using DHCP** (labeled as 1 in the image below) and then click the **Renew DHCP Lease** button (labeled as 2 in the image below) before clicking the **OK** button (labeled as 3 in the image below).
  

  1. After clicking **OK**, the main **Network** window will appear again and the IP Address shown will be one assigned by the AC1750, even though we are connected to the AC1200. We can tell that we are connected to the AC1750 through the AC1200 as the **Router** IP address listed in the **Network** window is the one for the AC1750 (**10.19.122.1**). Additionally, the IP address we were assigned is in the range of **10.19.122.2-255** indicating that AC1750's DHCP server assigned us an IP address. The image below contains an example IP address assigned by the AC1750, showing that the WDS was successfully bridged.
  

- Windows
  1. After connecting to the AC1200, open the **Network & Internet** settings and then click on **Change connection properties** which is boxed in red in the image below:
  

  1. At the bottom of the new window, click the **Edit** button under the **IP assignment:** section, boxed in red below:
  

  1. Click the drop-down menu with the text **Manual** (labeled as 1 in the image below) and change it to **Automatic (DHCP)** and then select **Save** (labeled as 2 in the image below).
  

  1. After clicking **Save**, scroll to the bottom of the page and under the **Properties** section you should see an IPv4 address that was assigned by the AC1750 as it is in the range **10.19.122.2-255**.
  

---
## Conclusion ##
This procedure should only need to be completed when moving the boat to a new location or when new wireless networks are introduced to the environment.

The bridged network is also not required to connect to the boat. Instead, when developing in the lab you can connect directly to the AC1750's wireless network (**TempleBoat_Onboard**) and this will likely yield better speeds when in close proximity. However, when testing in water, the bridged network will provide a better connection range.

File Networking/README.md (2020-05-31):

# Network Configuration Information #
## Network Hardware IP Addresses ##
| Device | Location | Function | IP |
| :--- |:---:| :--- | :---:|
| [TP-Link AC1750](https://www.tp-link.com/us/home-networking/wifi-router/archer-a7/) | Onboard | Main router for the boat | `10.19.121.1`|
| [GL-iNet GL-AR750](https://www.gl-inet.com/products/gl-ar750/) | Onboard | Provide internet connection to `tusecurewireless` or another WiFi network | `10.19.122.1` |
| [TP-Link AC1200](https://www.tp-link.com/us/home-networking/wifi-router/archer-a5/) | Shore | Create shore-side wireless bridged network | `10.19.123.1` |

## Reserved Device IP Addresses ##
| Hostname | Interface | IP |
| :--- |:---:| :---:|
| roboboat-Pi4 | Ethernet | `10.19.122.101` |
| Roboboat-TX2 | Ethernet | `10.19.122.102` |

# Network Maintenance & Additional Information #
## Restoring the Network ##
If the network is accidentally misconfigured, use the router's provided [backup files](RouterBackups/) to restore functionality. 

## Connecting to the Internet ##
The GL.iNet GL-AR750 connects all network devices to the internet. Though its management portal, a connection to the `tusecurewireless` network can be established. Follow the instructions in the [Connect_to_Internet.md](Connect_to_Internet.md) file to establish an internet connection.

## Modifying the WiFi Bridge ##
The WDS bridge may need to be modified if the boat is moved to a new location or if wireless networks are added to the boat's environment. A [guide](Modifying_WiFi_Bridge.md) is provided for this procedure.

## Hardware Documentation ##
* TP-Link AC1750 (Archer A7): | [User Guide](RouterManuals/AC1750A7_UserGuide.pdf) | [Quick Installation Guide](RouterManuals/AC1750A7_QuickInstallationGuide.pdf) | [Datasheet](RouterManuals/AC1750A7_DataSheet.pdf) |
* TP-Link AC1200 (Archer A5): | [User Guide](RouterManuals/AC1200A5_UserGuide.pdf) | [Quick Installation Guide](RouterManuals/AC1200A5_QuickInstallationGuide.pdf) |
* GL-iNet GL-AR750: | [Docs Website](https://docs.gl-inet.com/en/3/setup/travel_ac_router/first-time_setup/) | [Docs Website - PDF Version](RouterManuals/GL-AR750_UserGuide.pdf) |

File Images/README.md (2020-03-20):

# Power Distribution #
 
 
<!--
![](Hardware_PowerDistribution/Hardware_PowerDistribution_ExteriorTop.JPG)
![](Hardware_PowerDistribution/Hardware_PowerDistribution_Interior.JPG)
![](Hardware_PowerDistribution/Hardware_PowerDistribution_ExteriorFront.JPG)
![](Hardware_PowerDistribution/Hardware_PowerDistribution_ExteriorBack.JPG)
--->
---
# Motor Control, GPS, and IMU #
 
<!--
![](Hardware_TeensyBoard/Hardware_TeensyBoard_Assembled.JPG)
![](Hardware_TeensyBoard/Hardware_TeensyBoard_Disassembled.JPG)
--->
---
# Battery Monitor #
 
 

<!--
![](Hardware_BatteryMonitor/Hardware_BatteryMonitor_Aassembled.JPG)
![](Hardware_BatteryMonitor/Hardware_BatteryMonitor_LowerBoard.JPG)
![](Hardware_BatteryMonitor/Hardware_BatteryMonitor_DisassembledTop.JPG)
![](Hardware_BatteryMonitor/Hardware_BatteryMonitor_DisassembledBottom.jpg)
--->
---
# Emergency Transmitter #
 

<!--
![](Hardware_EmergencyTransmitter/Hardware_EmergencyTransmitter_ExteriorFront.jpg)
![](Hardware_EmergencyTransmitter/Hardware_EmergencyTransmitter_Interior.JPG)
![](Hardware_EmergencyTransmitter/Hardware_EmergencyTransmitter_ExteriorTop.jpg)
--->
---
# Emergency Receiver #
 

<!--
![](Hardware_EmergencyReceiver/Hardware_EmergencyReceiver_Front.JPG)
![](Hardware_EmergencyReceiver/Hardware_EmergencyReceiver_Interior.JPG)
![](Hardware_EmergencyReceiver/Hardware_EmergencyReceiver_Back.JPG)
--->
---
# Test Videos #
### Video: Temple RoboBoat 2020 - Pool Test 01a (10-27-2019) ###
Temple RoboBoat 2020 - Pool Test 01a (10-27-2019) (http://www.youtube.com/watch?v=3CQom3ANsao)

### Video: Temple RoboBoat 2020 - Pool Test 01b (10-27-2019) ###
Temple RoboBoat 2020 - Pool Test 01b (10-27-2019) (http://www.youtube.com/watch?v=m9lShAPSa88)

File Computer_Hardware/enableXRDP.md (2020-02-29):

# XRDP Setup on the Jetson TX2 with Jetpack 4.3

Disclaimer: We are still not exactly sure how this works, but the solution presented below is the result of combining multiple other solutions we found though Google. 

1. Install a new desktop environment (xfce4 in this demo). We were not able to get this to work with the pre-installed desktop environment.
```
sudo apt update
sudo apt install xfce4 xfce4-goodies xorg dbus-x11 x11-xserver-utils
```

2. Install XRDP and add the `xrdp` user to the `ssl-cert` group.
```
sudo apt install xrdp
sudo adduser xrdp ssl-cert
```

3. Configure XDRP to use the xfce4 desktop environment we installed in Step 1.
   * Add `exec startxfce4` to the end of the `/etc/xrdp/xrdp.ini` file.
   * `echo xfce4-session > ~/.xsession`

4. Restart XRDP
```
sudo systemctl restart xrdp
```

Now attempt to log into XRDP for the first time!





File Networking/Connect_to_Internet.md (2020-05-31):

# How to connect the boat's network to the internet #
---

1. Navigate to the admin portal (located at [10.19.121.1](http://10.19.121.1) if the router was configured using the backup provided in the [RouterBackups](RouterBackups/) folder.

---

2. Click the "**Scan**" under the "**Repeater** section of the "**INTERNET**" page as can be seen below:



---

3. Wait for the network scan to complete:



---

4. Select the "**tusecurewireless**" network or any other network that you wish to connect to and enter your credentials or the network password.



---

If this connection process fails, try restarting the router. If it still fails, refer to the [docs provided by GL-iNet](https://docs.gl-inet.com/en/3/setup/travel_ac_router/first-time_setup/).

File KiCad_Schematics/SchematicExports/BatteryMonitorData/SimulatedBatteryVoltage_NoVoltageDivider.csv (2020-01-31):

Time | 0.000000 | 0.000300 | 0.000600 | 0.001200 | 0.002400 | 0.004800 | 0.009600 | 0.019200 | 0.038400 | 0.076800 | 0.136800 | 0.196800 | 0.256800 | 0.316800 | 0.376800 | 0.436800 | 0.496800 | 0.556800 | 0.616800 | 0.676800 | 0.736800 | 0.796800 | 0.856800 | 0.916800 | 0.976800 | 1.000000 | 1.006000 | 1.018000 | 1.042000 | 1.090000 | 1.150000 | 1.210000 | 1.270000 | 1.330000 | 1.390000 | 1.450000 | 1.510000 | 1.570000 | 1.630000 | 1.690000 | 1.750000 | 1.810000 | 1.870000 | 1.930000 | 1.990000 | 2.000000 | 2.006000 | 2.018000 | 2.042000 | 2.090000 | 2.150000 | 2.210000 | 2.270000 | 2.330000 | 2.390000 | 2.450000 | 2.510000 | 2.570000 | 2.630000
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

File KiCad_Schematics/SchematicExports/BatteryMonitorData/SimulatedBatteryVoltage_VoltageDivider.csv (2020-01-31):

Time | 0.000000 | 0.000300 | 0.000600 | 0.001200 | 0.002400 | 0.004800 | 0.009600 | 0.019200 | 0.038400 | 0.076800 | 0.136800 | 0.196800 | 0.256800 | 0.316800 | 0.376800 | 0.436800 | 0.496800 | 0.556800 | 0.616800 | 0.676800 | 0.736800 | 0.796800 | 0.856800 | 0.916800 | 0.976800 | 1.000000 | 1.006000 | 1.018000 | 1.042000 | 1.090000 | 1.150000 | 1.210000 | 1.270000 | 1.330000 | 1.390000 | 1.450000 | 1.510000 | 1.570000 | 1.630000 | 1.690000 | 1.750000 | 1.810000 | 1.870000 | 1.930000 | 1.990000 | 2.000000 | 2.006000 | 2.018000 | 2.042000 | 2.090000 | 2.150000 | 2.210000 | 2.270000 | 2.330000 | 2.390000 | 2.450000 | 2.510000 | 2.570000 | 2.630000
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

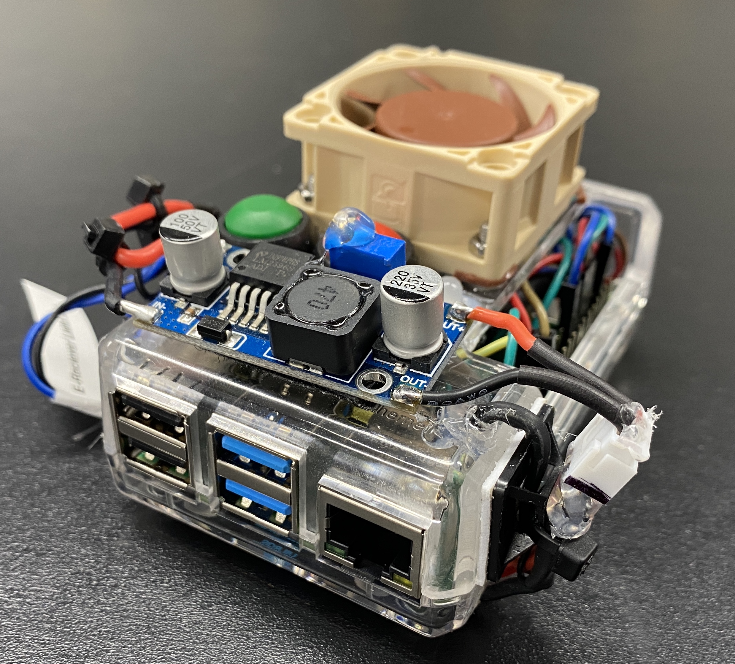
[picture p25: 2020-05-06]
Images/Hardware_Compute/RPi4_TopFront.jpg

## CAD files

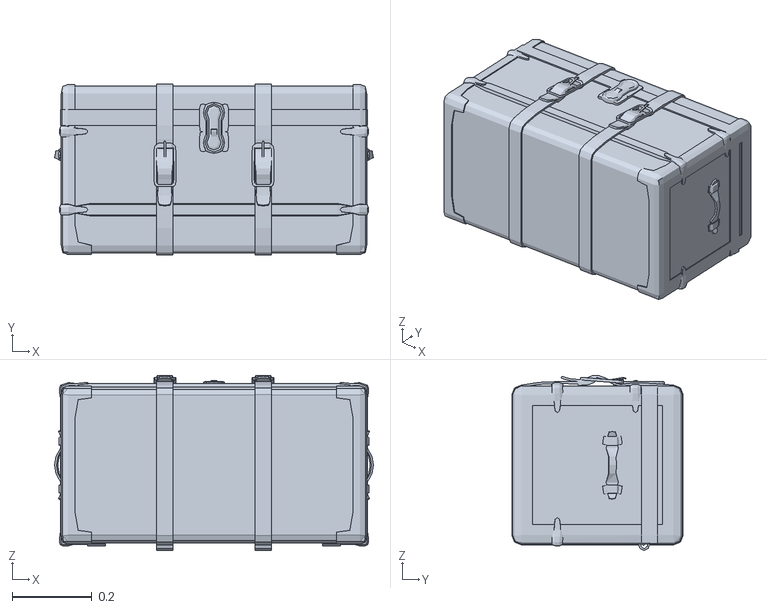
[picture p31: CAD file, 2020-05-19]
Boat_Website/src/xeogl-master/examples/models/obj/chest/Chest.obj
0.802 x 0.431 x 0.44

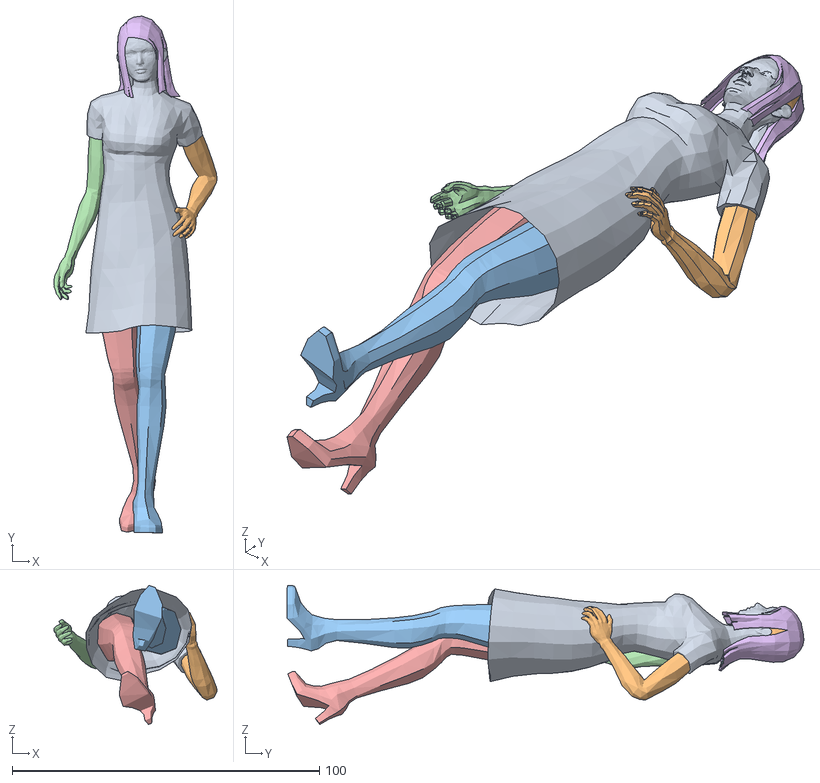
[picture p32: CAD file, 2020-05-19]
Boat_Website/src/xeogl-master/examples/models/obj/female02/female02.obj
53.0 x 168.2 x 45.2
mesh1.002_mesh1-geometry
mesh2.002_mesh2-geometry
mesh3.002_mesh3-geometry
mesh4.002_mesh4-geometry
mesh5.002_mesh5-geometry
mesh6.002_mesh6-geometry
mesh7.002_mesh7-geometry
mesh8.002_mesh8-geometry
mesh9.002_mesh9-geometry
mesh10.002_mesh10-geometry

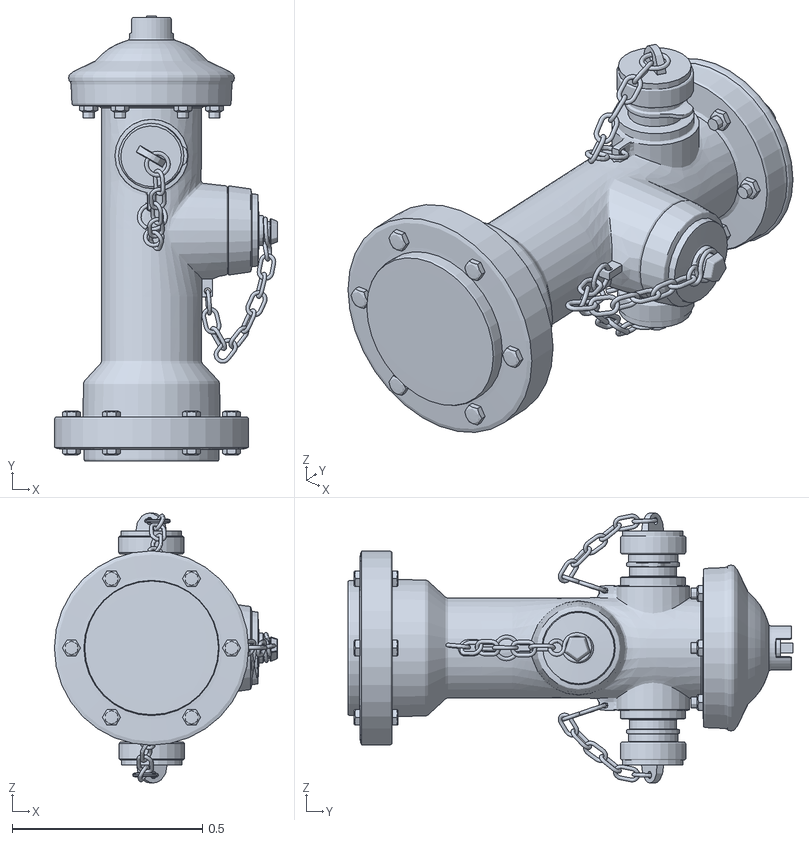
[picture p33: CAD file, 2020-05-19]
Boat_Website/src/xeogl-master/examples/models/obj/fireHydrant/FireHydrantMesh.obj
0.587 x 1.17 x 0.71

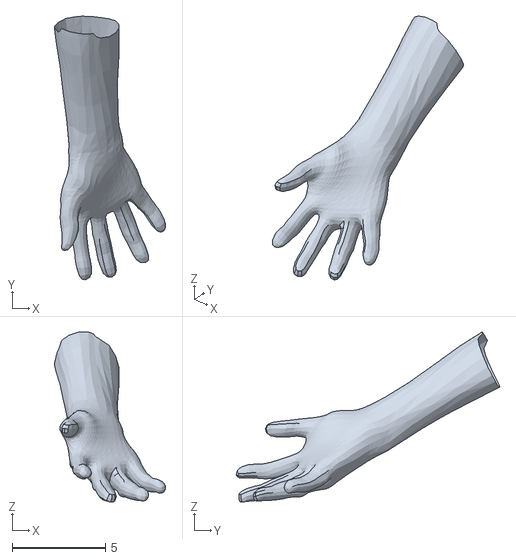
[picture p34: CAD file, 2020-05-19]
Boat_Website/src/xeogl-master/examples/models/obj/hand/hand.obj
5.97 x 14.1 x 9.10

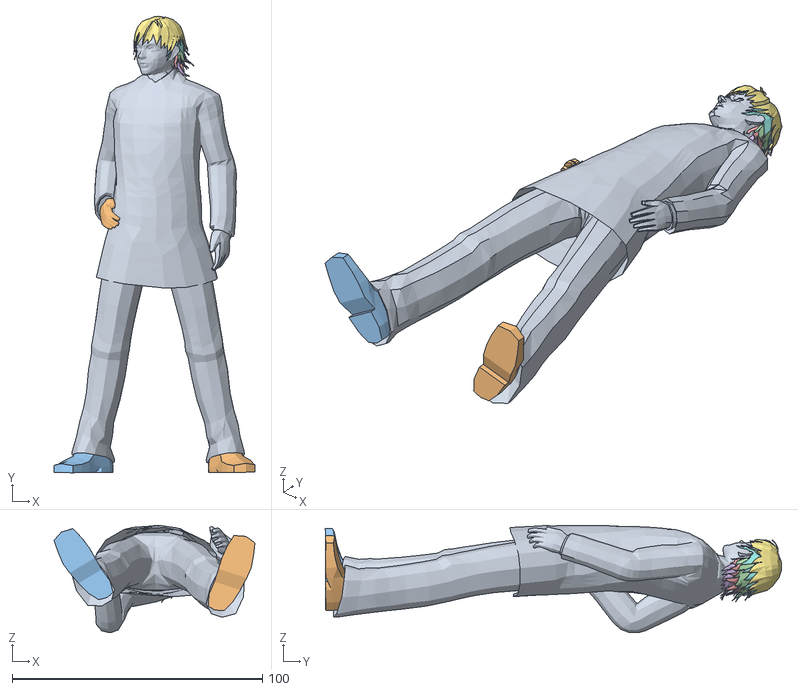
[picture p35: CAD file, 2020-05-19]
Boat_Website/src/xeogl-master/examples/models/obj/male02/male02.obj
80.4 x 182.5 x 42.9
mesh1.002_mesh1-geometry
mesh2.002_mesh2-geometry
mesh3.002_mesh3-geometry
mesh4.002_mesh4-geometry
mesh5.002_mesh5-geometry
mesh6.002_mesh6-geometry
mesh7.002_mesh7-geometry
mesh8.002_mesh8-geometry
mesh9.002_mesh9-geometry
mesh10.002_mesh10-geometry

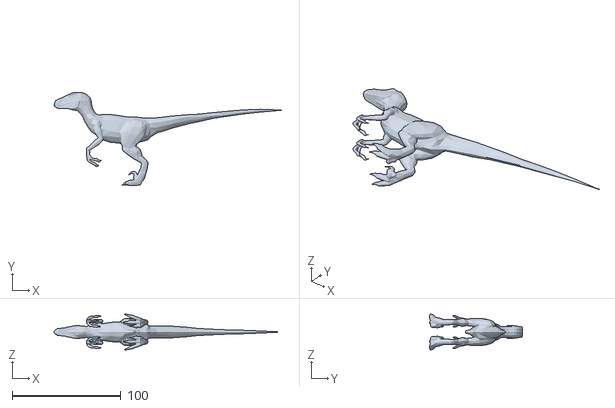
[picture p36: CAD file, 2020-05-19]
Boat_Website/src/xeogl-master/examples/models/obj/raptor/raptor.obj
211.0 x 86.0 x 33.0

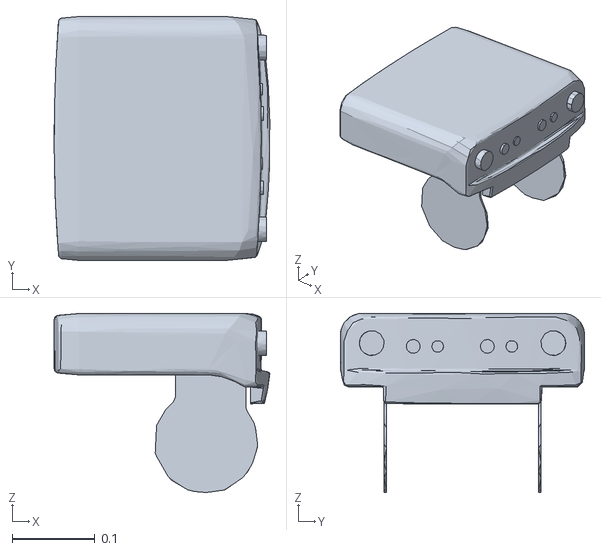
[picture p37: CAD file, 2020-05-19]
Boat_Website/src/xeogl-master/examples/models/stl/ascii/pr2_head_tilt.stl
0.261 x 0.296 x 0.217

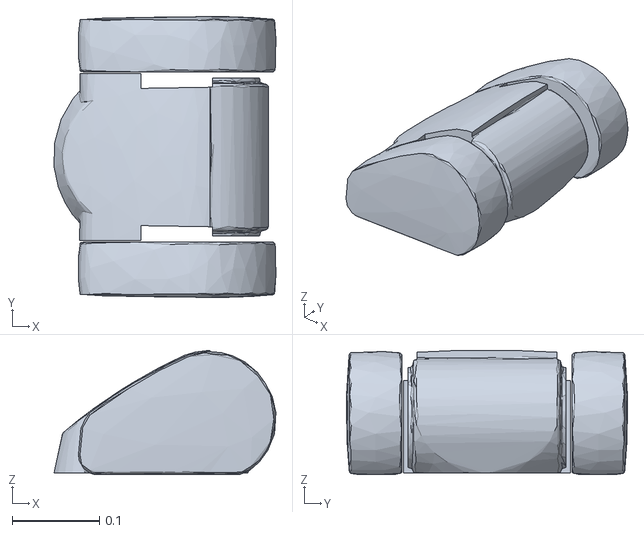
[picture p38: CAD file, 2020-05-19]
Boat_Website/src/xeogl-master/examples/models/stl/binary/pr2_head_pan.stl
0.254 x 0.321 x 0.142

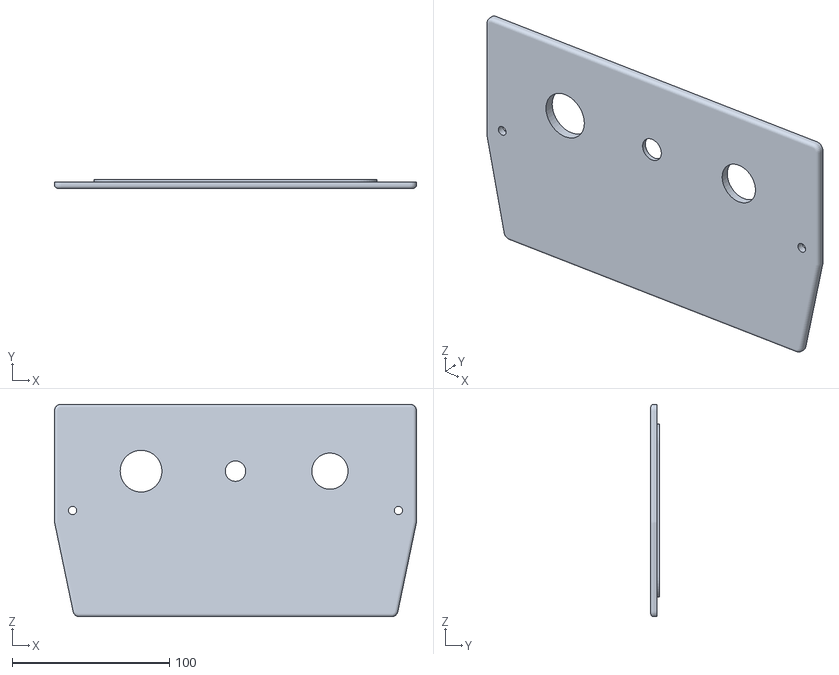
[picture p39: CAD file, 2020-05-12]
CAD_Files/CableCover/PartFiles/CableCover_STL.stl
230.0 x 5.50 x 135.0

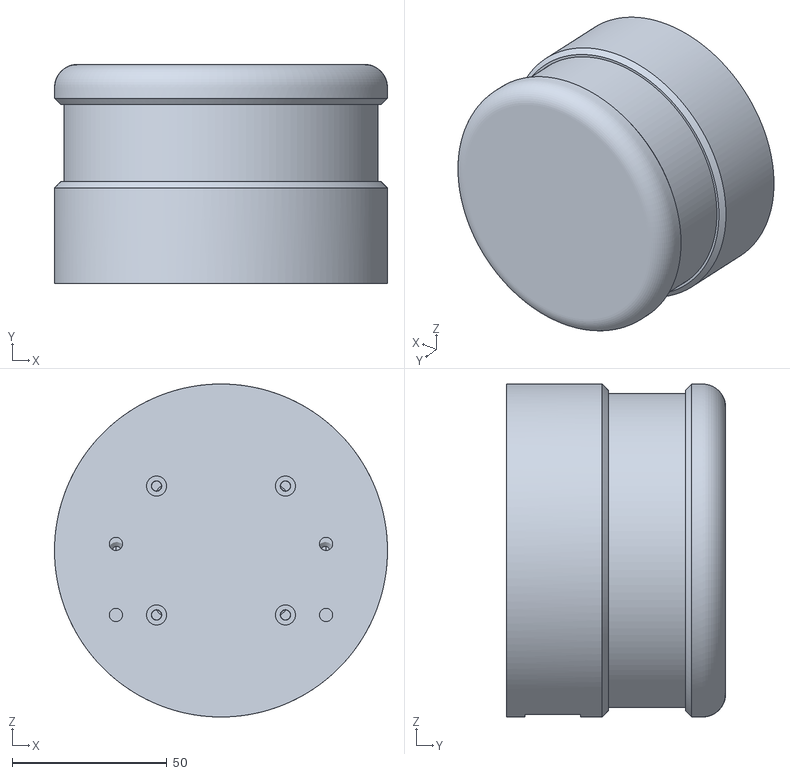
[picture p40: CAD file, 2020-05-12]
CAD_Files/LidarEnclosure/PartFiles/LidarEnclosure_STL.stl
107.8 x 71.0 x 107.7

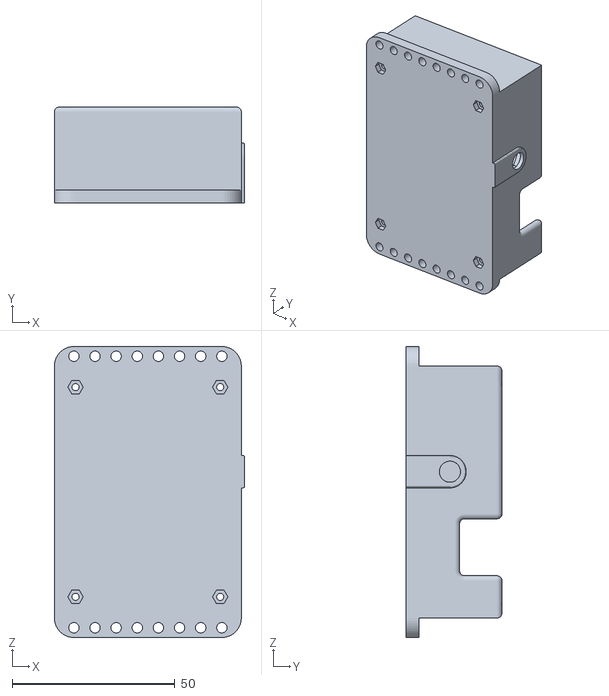
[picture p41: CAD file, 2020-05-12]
CAD_Files/TeensyEnclosure/PartFiles/TeensyEnclosure_STL.stl
58.5 x 29.5 x 89.5

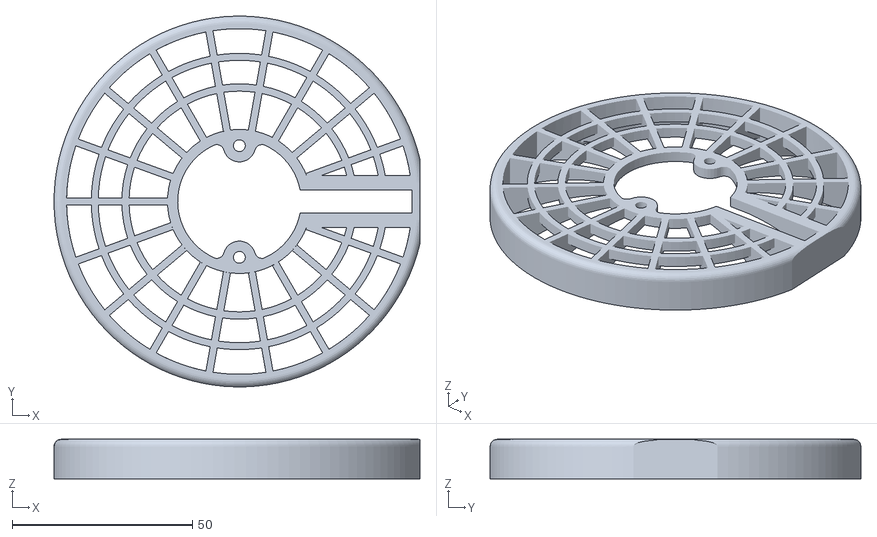
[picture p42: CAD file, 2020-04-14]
CAD_Files/Z-Other/Front_Intake_Guard_for_T200_Thruster/files/intake2d.stl
101.6 x 102.9 x 11.0

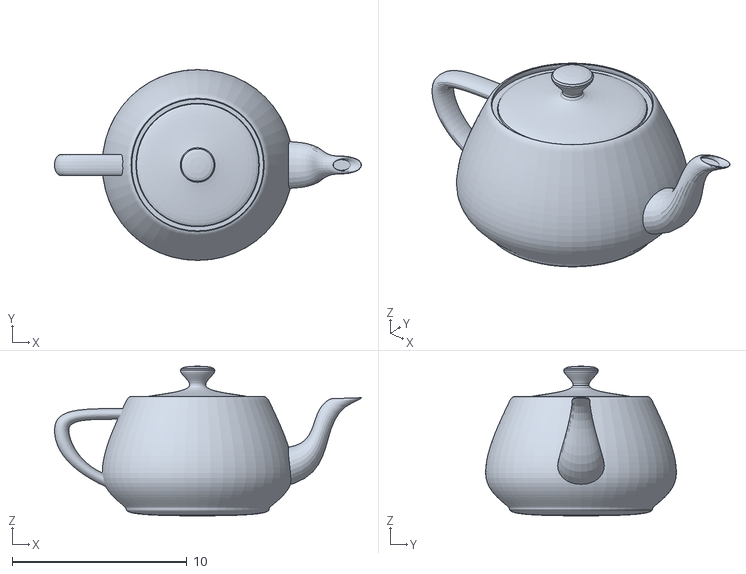
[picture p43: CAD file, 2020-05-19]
Boat_Website/src/xeogl-master/examples/models/stl/binary/Utah_teapot_(solid).stl
17.6 x 10.9 x 8.57

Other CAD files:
Boat_Website/src/xeogl-master/examples/models/obj/female02/female02_vertex_colors.obj
Boat_Website/src/xeogl-master/examples/models/stl/ascii/pr2_head_pan.stl
CAD_Files/CableCover/PartFiles/CableCover_STEP.step
CAD_Files/LidarEnclosure/PartFiles/LidarEnclosure_STEP.step
CAD_Files/TeensyEnclosure/PartFiles/TeensyEnclosure_STEP.step
Boat_Website/src/xeogl-master/examples/models/stl/ascii/slotted_disk.stl
Boat_Website/src/xeogl-master/examples/models/stl/binary/colored.stl
Boat_Website/src/xeogl-master/examples/models/stl/binary/pr2_head_tilt.stl
Boat_Website/src/xeogl-master/examples/models/stl/binary/spurGear.stl
CAD_Files/CableCover/PartFiles/CableCover_AutodeskInventor.ipt
CAD_Files/CableCover/PartFiles/CableCover_Fusion.f3d
CAD_Files/LidarEnclosure/PartFiles/LidarEnclosure_Fusion.f3z
CAD_Files/MotorMounts/PartFiles/MotorMount_Fusion.f3z
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

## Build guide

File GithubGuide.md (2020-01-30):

## Initial GitHub setup

(1) Navigate to the folder in your terminal that you want the repository to be locally stored at. 

(2) Clone the repository to your computer:
```
git clone [INSERT REPOSITORY ADDRESS]
```

## Updating your local repository after changes have been made by others

(1) Navigate to the folder containing the repository in your terminal

(2) Pull updates from the GitHub
```
git pull
```

## Updating the repository with new files or changes you made to existing files

(1) Navigate to the folder containing the repository in your terminal

(2) Perform a `git pull` command to update your local copy of the repository with changes that others may have made

(3) View your files that have been added/edited since your last 'push' that need to be updated in the repository
```
git status
```

(4a) Add your files that you want to commit (update) in the GitHub repository
```
git add [INSERT FILES/DIRECTORIES HERE    MULTIPLE FILES/DIRECTORIES CAN BE SEPARATED BY SAPCES]
```

(4b) Remove files from tracking that you never again wish to commit to the GitHub repository (optional - not always required)
```
git rm [INSERT FILES/DIRECTORIES HERE    MULTIPLE FILES/DIRECTORIES CAN BE SEPARATED BY SAPCES]
```

(5) Add a messge to the commit to let your team members know what you added/changed in the repository
```
git commit -m "[ADD MESSAGE ABOUT THE FILE(S) BEING COMMITTED/UPDATED HERE]"
```

(6) Push the changes to the repository and make your edits visible to your team members
```
git push
```

## Remove deleted files from tracking
```
git add -u .
git commit -m "removing deleted files from tracking"
git push
```

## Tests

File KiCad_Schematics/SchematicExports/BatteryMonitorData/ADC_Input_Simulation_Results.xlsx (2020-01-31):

Raw Cell Voltages | Time | 0 | 0.0003 | 0.0006 | 0.0012 | 0.0024 | 0.0048 | 0.0096 | 0.0192 | 0.0384 | 0.0768 | 0.1368 | 0.1968 | 0.2568 | 0.3168 | 0.3768 | 0.4368 | 0.4968 | 0.5568 | 0.6168 | 0.6768 | 0.7368 | 0.7968 | 0.8568 | 0.9168 | 0.9768 | 1 | 1.006 | 1.018 | 1.042 | 1.09 | 1.15 | 1.21 | 1.27 | 1.33 | 1.39 | 1.45 | 1.51 | 1.57 | 1.63 | 1.69 | 1.75 | 1.81 | 1.87 | 1.93 | 1.99 | 2 | 2.006 | 2.018 | 2.042 | 2.09 | 2.15 | 2.21 | 2.27 | 2.33 | 2.39 | 2.45 | 2.51 | 2.57
 | V(B1_C1) | 3 | 3 | 3 | 3 | 3 | 3 | 3 | 3 | 3 | 3 | 3 | 3 | 3 | 3 | 3 | 3 | 3 | 3 | 3 | 3 | 3 | 3 | 3 | 3 | 3 | 3 | 3.0072 | 3.0216 | 3.0504 | 3.108 | 3.18 | 3.252 | 3.324 | 3.396 | 3.468 | 3.54 | 3.612 | 3.684 | 3.756 | 3.828 | 3.9 | 3.972 | 4.044 | 4.116 | 4.188 | 4.2 | 4.2 | 4.2 | 4.2 | 4.2 | 4.2 | 4.2 | 4.2 | 4.2 | 4.2 | 4.2 | 4.2 | 4.2
 | V(B1_C2) | 6 | 6 | 6 | 6 | 6 | 6 | 6 | 6 | 6 | 6 | 6 | 6 | 6 | 6 | 6 | 6 | 6 | 6 | 6 | 6 | 6 | 6 | 6 | 6 | 6 | 6 | 6.0144 | 6.0432 | 6.1008 | 6.216 | 6.36 | 6.504 | 6.648 | 6.792 | 6.936 | 7.08 | 7.224 | 7.368 | 7.512 | 7.656 | 7.8 | 7.944 | 8.088 | 8.232 | 8.376 | 8.4 | 8.4 | 8.4 | 8.4 | 8.4 | 8.4 | 8.4 | 8.4 | 8.4 | 8.4 | 8.4 | 8.4 | 8.4
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

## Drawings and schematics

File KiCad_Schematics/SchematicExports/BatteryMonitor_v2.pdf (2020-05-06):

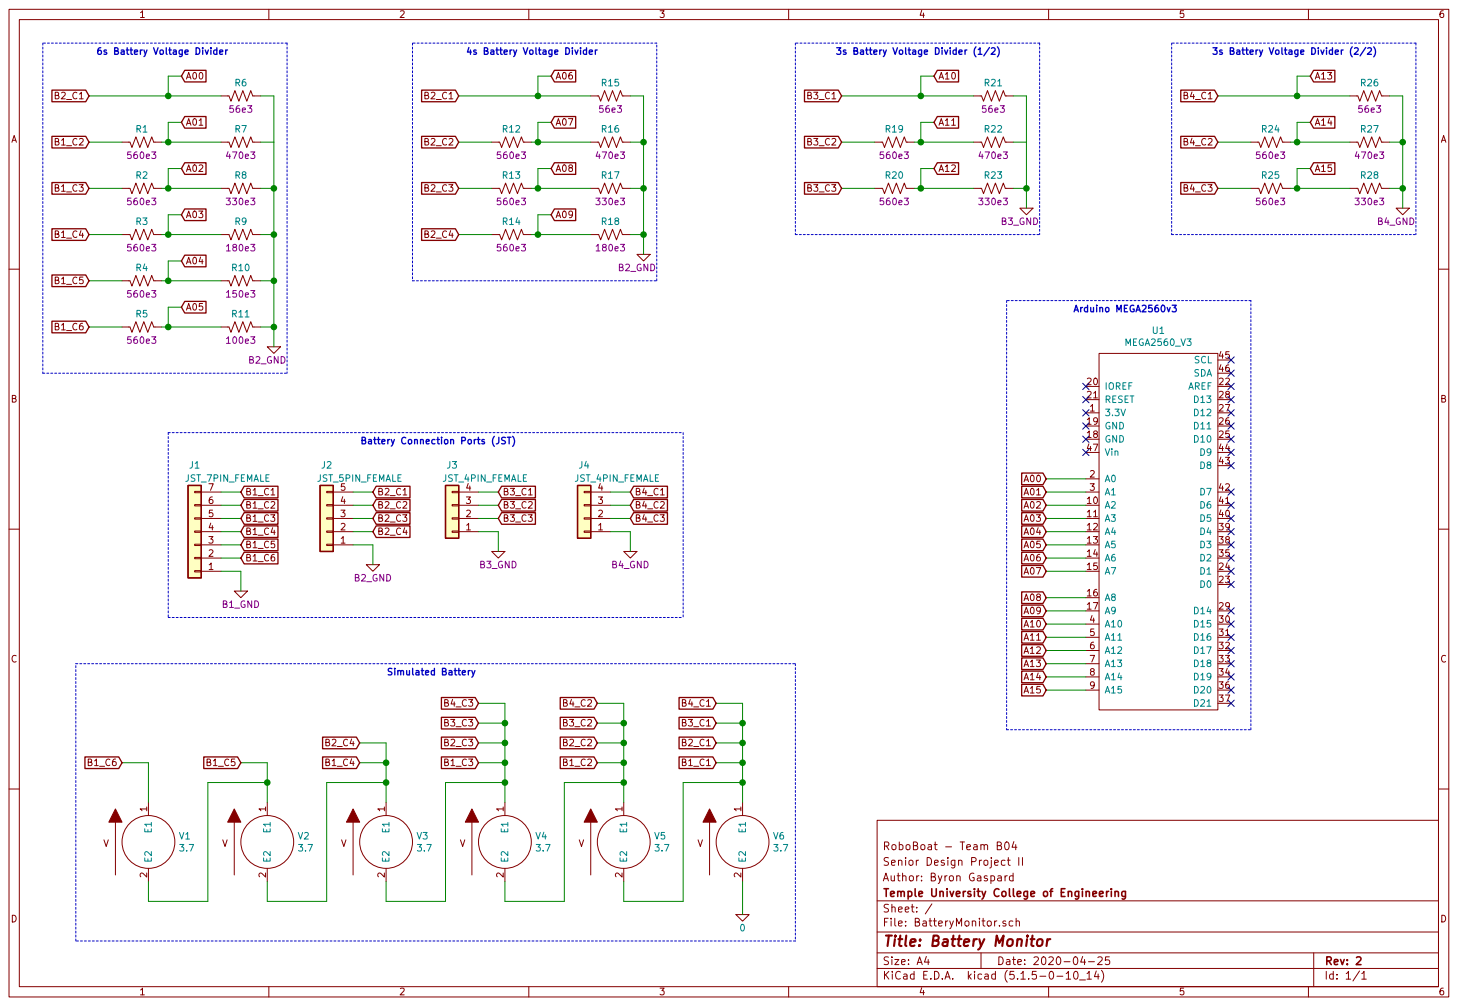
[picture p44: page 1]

Battery Connection Ports (JST)

Senior Design Project II RoboBoat - Team B04

Author: Byron Gaspard
File: BatteryMonitor.sch Sheet: / Temple University College of Engineering

Id: 1/1 Title: Battery Monitor

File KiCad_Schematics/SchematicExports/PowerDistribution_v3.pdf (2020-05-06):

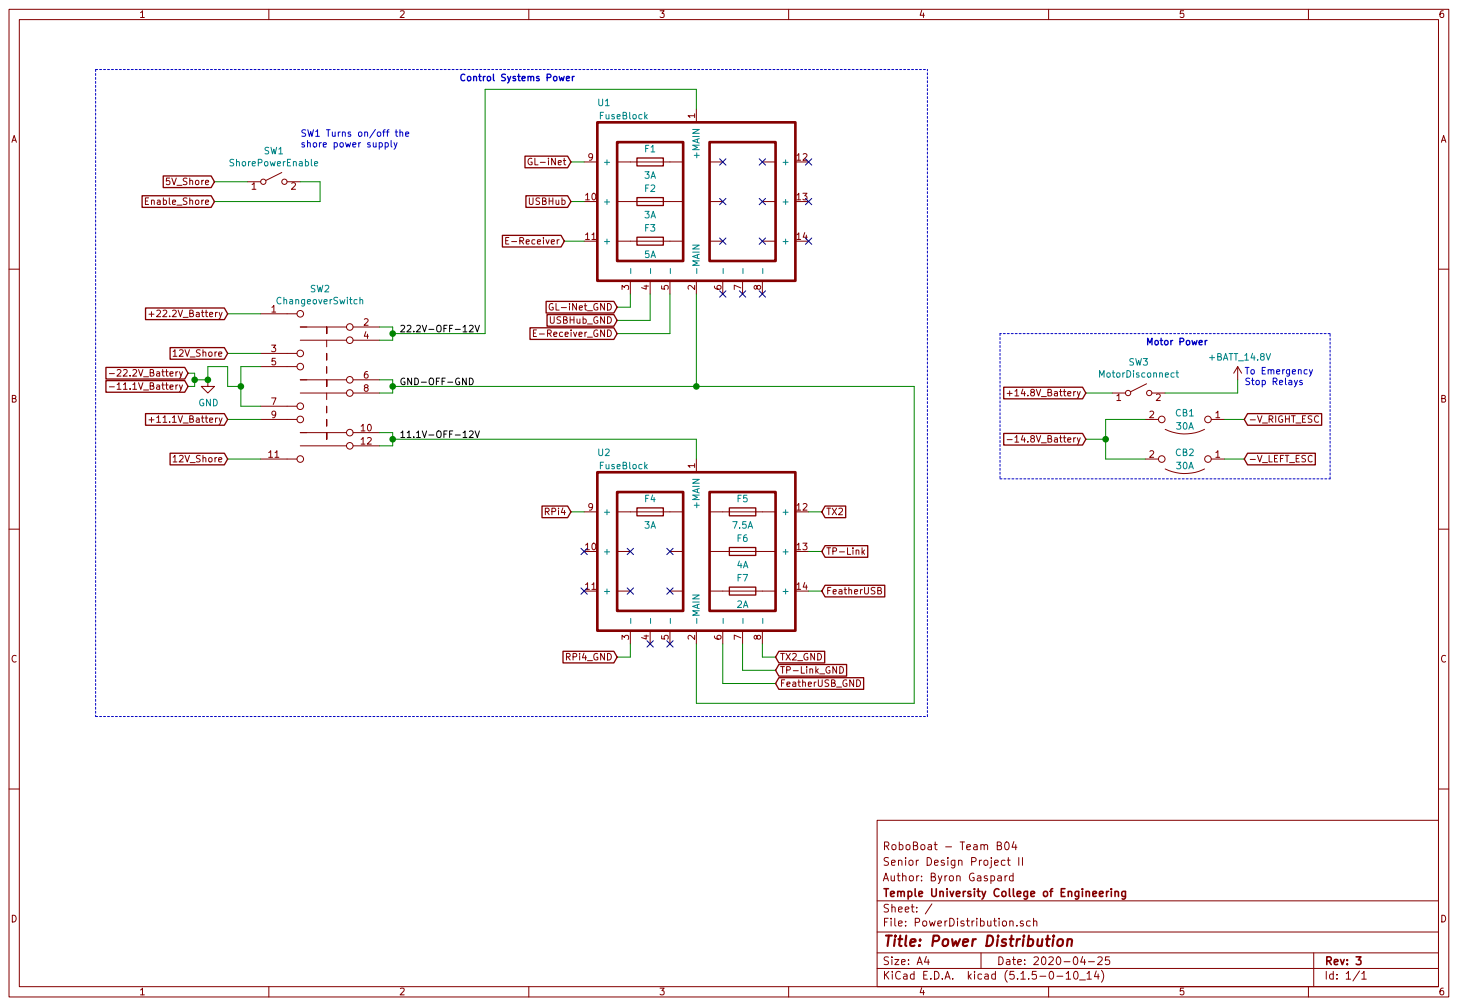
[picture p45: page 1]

SW1 Turns on/off the shore power supply

Senior Design Project II RoboBoat - Team B04

Author: Byron Gaspard
File: PowerDistribution.sch Sheet: / Temple University College of Engineering

Id: 1/1 Title: Power Distribution

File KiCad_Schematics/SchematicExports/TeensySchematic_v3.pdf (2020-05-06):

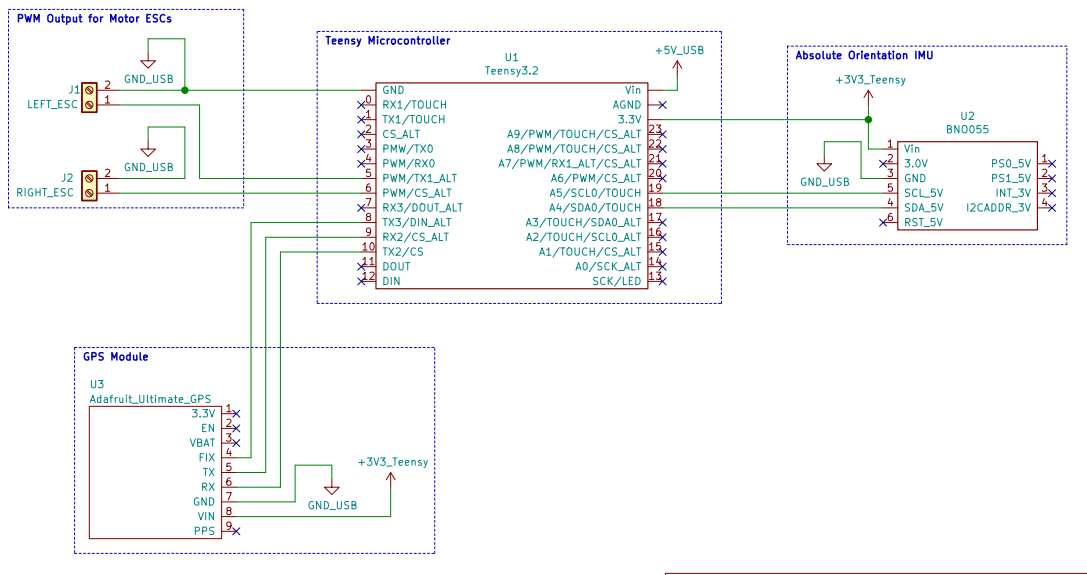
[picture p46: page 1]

PWM Output for Motor ESCs

Author: Byron Gaspard
File: TeensySchematic.sch Sheet: / Temple University College of Engineering

Id: 1/1 Title: Teensy Motor Control, GPS, and IMU Board

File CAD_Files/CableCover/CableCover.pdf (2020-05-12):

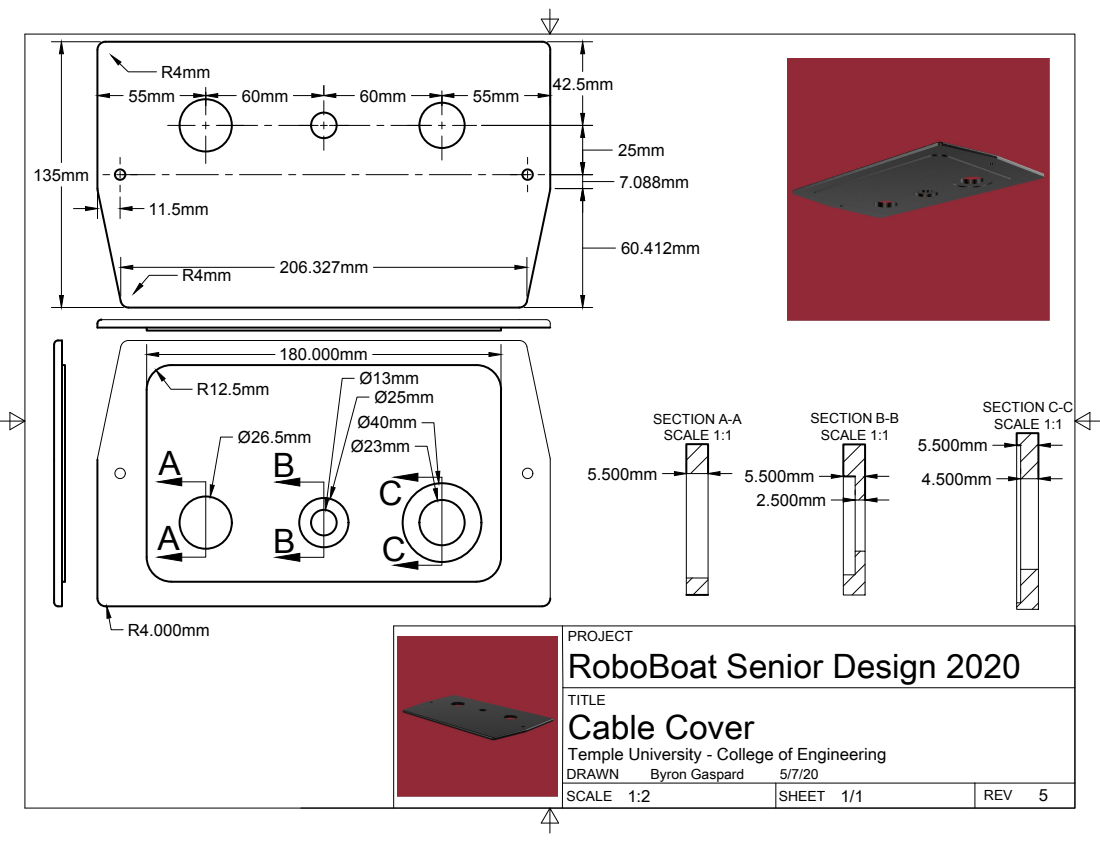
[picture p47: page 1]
SCALE 1:2; SHEET 1/1; REV; Byron Gaspard; Cable Cover; SECTION A-A SCALE 1:1; SECTION B-B SCALE 1:1; SECTION C-C SCALE 1:1

PROJECT
RoboBoat Senior Design 2020

Temple University - College of Engineering
DRAWN

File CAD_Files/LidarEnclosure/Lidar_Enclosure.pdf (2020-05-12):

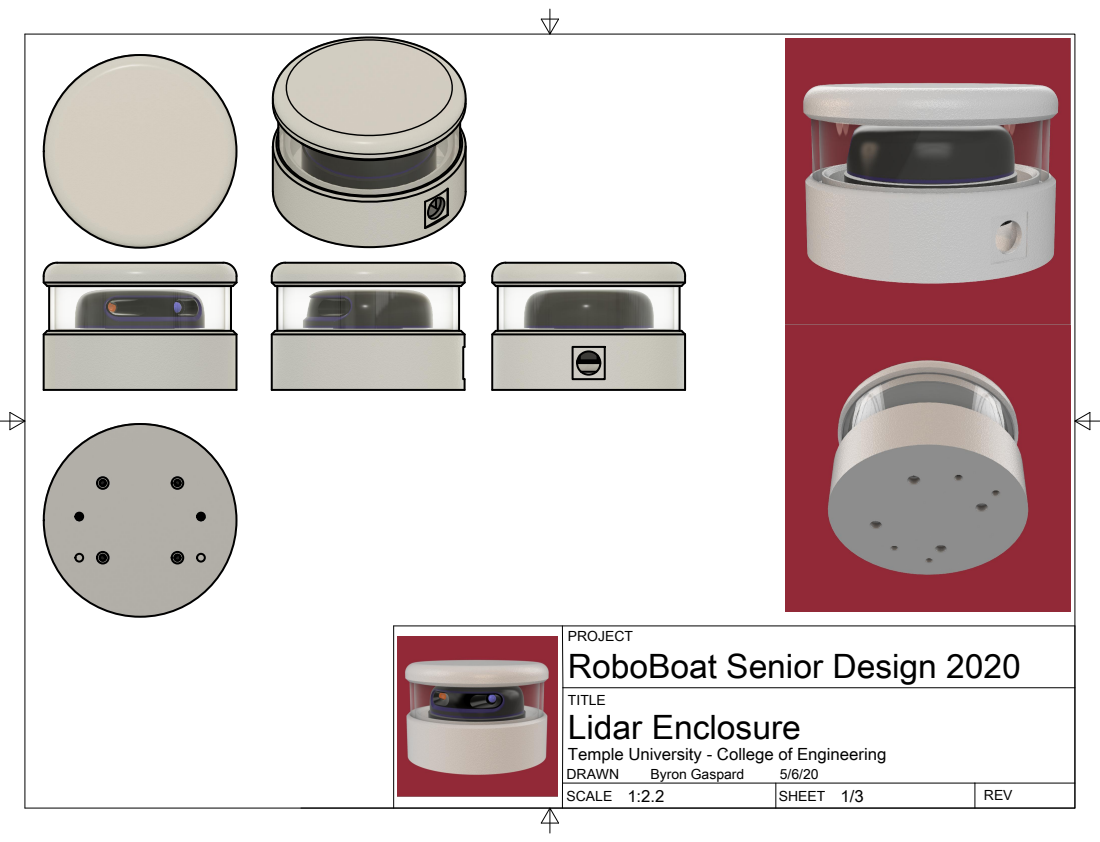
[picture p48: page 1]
SCALE 1:2.2; SHEET 1/3; REV; Byron Gaspard; Lidar Enclosure

PROJECT
RoboBoat Senior Design 2020

Temple University - College of Engineering
DRAWN

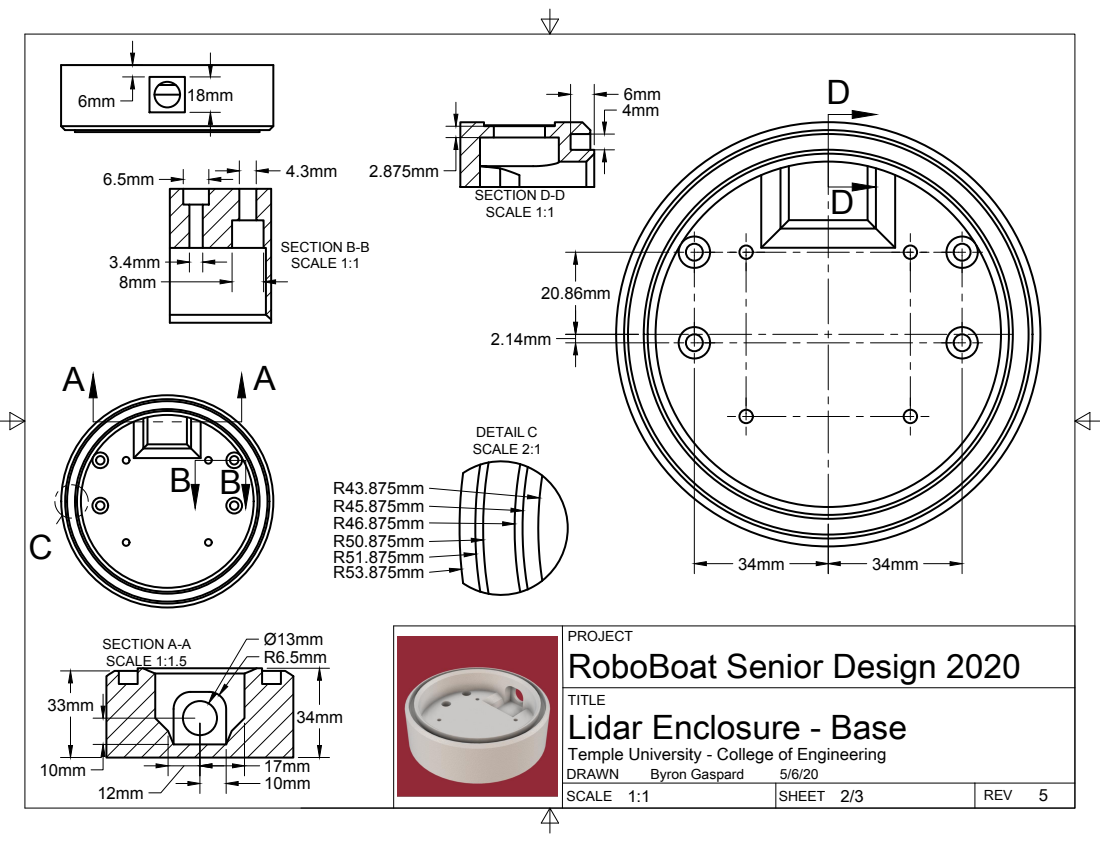
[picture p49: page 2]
SCALE 1:1; SHEET 2/3; REV; Byron Gaspard; SECTION A-A SCALE 1:1.5; DETAIL C SCALE 2:1; SECTION B-B SCALE 1:1; SECTION D-D SCALE 1:1

PROJECT
RoboBoat Senior Design 2020

TITLE
Lidar Enclosure - Base

Temple University - College of Engineering
DRAWN

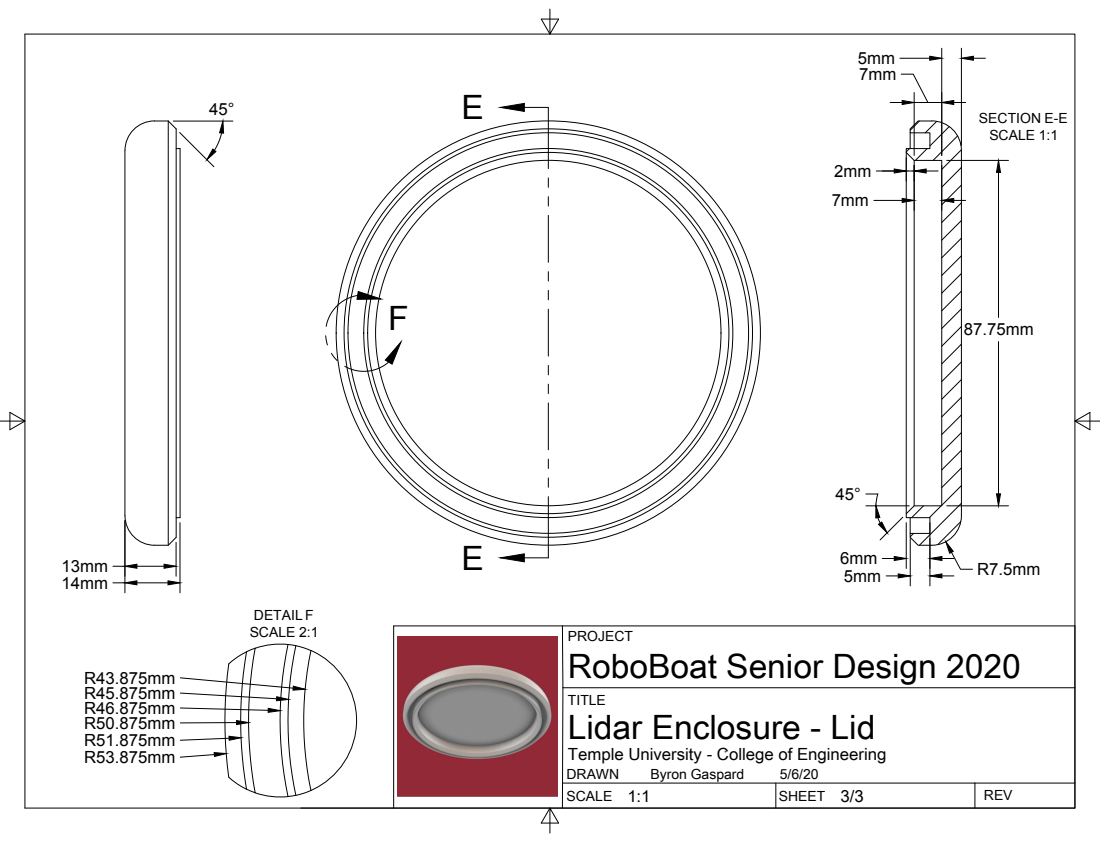
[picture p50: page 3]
SCALE 1:1; SHEET 3/3; REV; Byron Gaspard; SECTION E-E; DETAIL F SCALE 2:1

PROJECT
RoboBoat Senior Design 2020

TITLE
Lidar Enclosure - Lid

Temple University - College of Engineering
DRAWN

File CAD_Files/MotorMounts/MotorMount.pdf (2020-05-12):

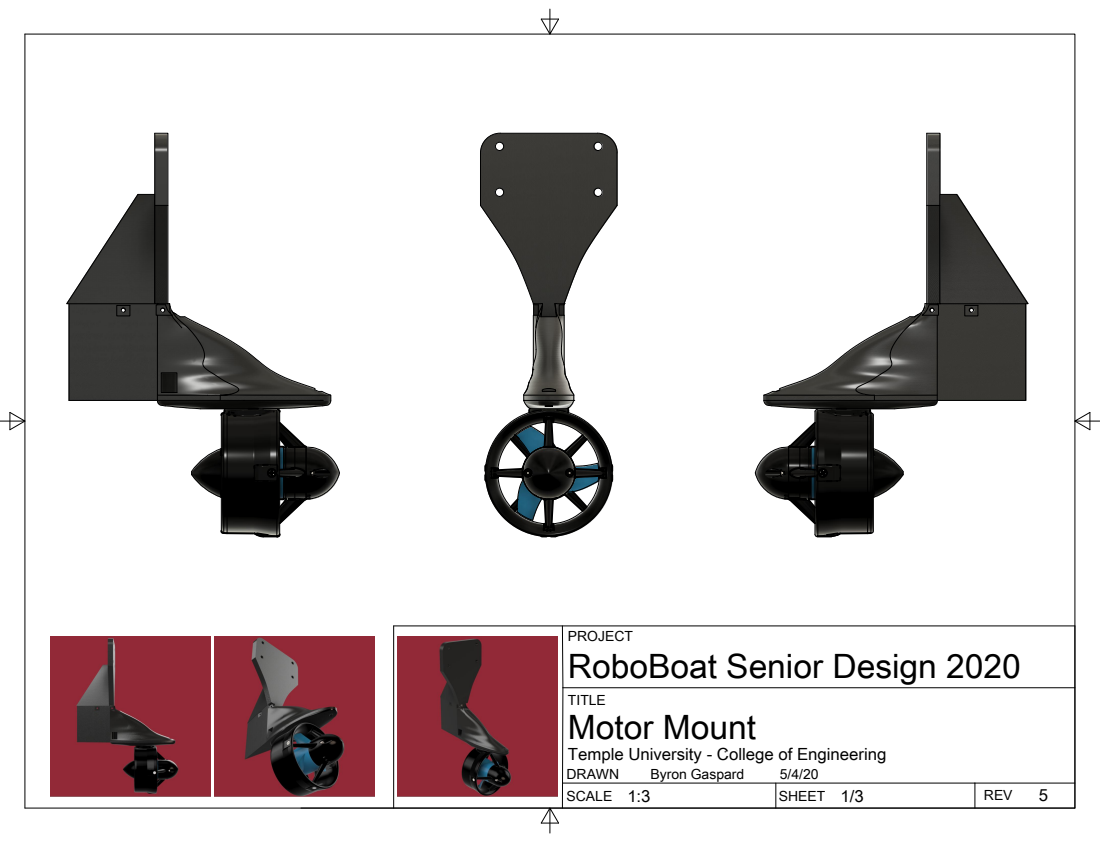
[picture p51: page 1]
SCALE 1:3; SHEET 1/3; REV; Byron Gaspard; Motor Mount

PROJECT
RoboBoat Senior Design 2020

Temple University - College of Engineering
DRAWN

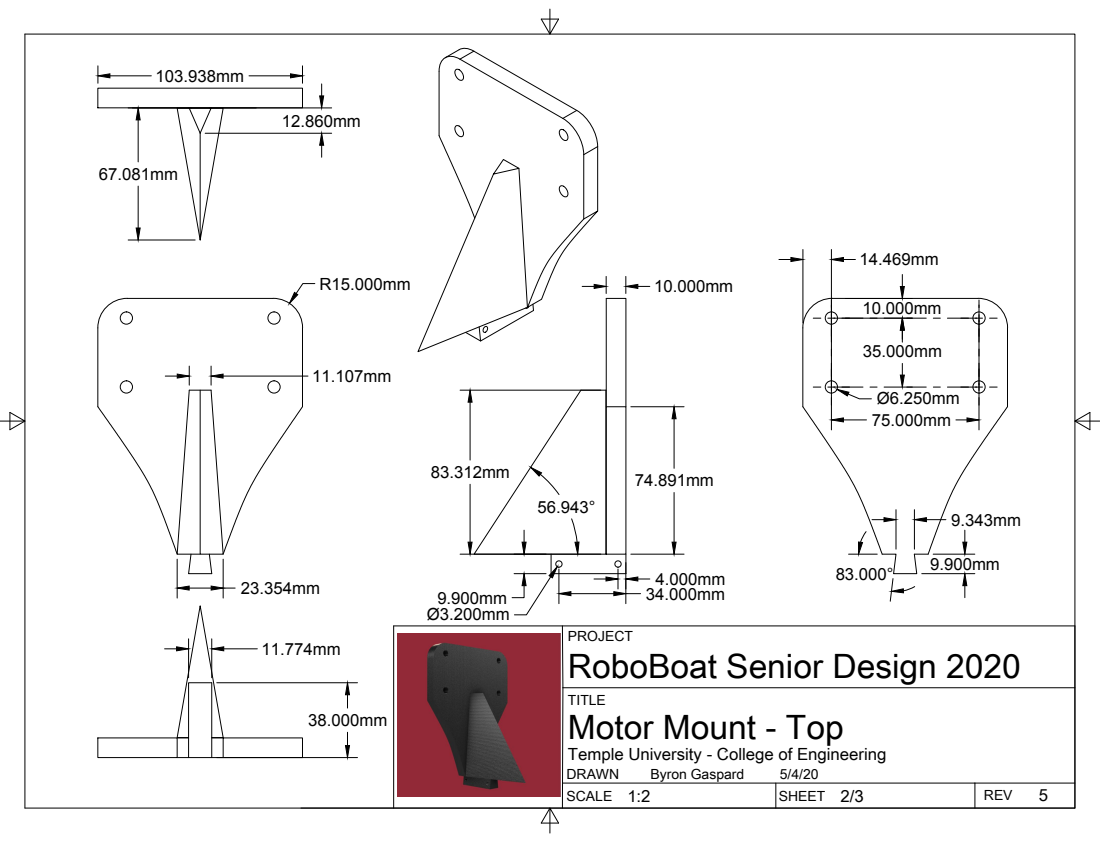
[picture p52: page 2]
SCALE 1:2; SHEET 2/3; REV; Byron Gaspard

PROJECT
RoboBoat Senior Design 2020

TITLE
Motor Mount - Top

Temple University - College of Engineering
DRAWN

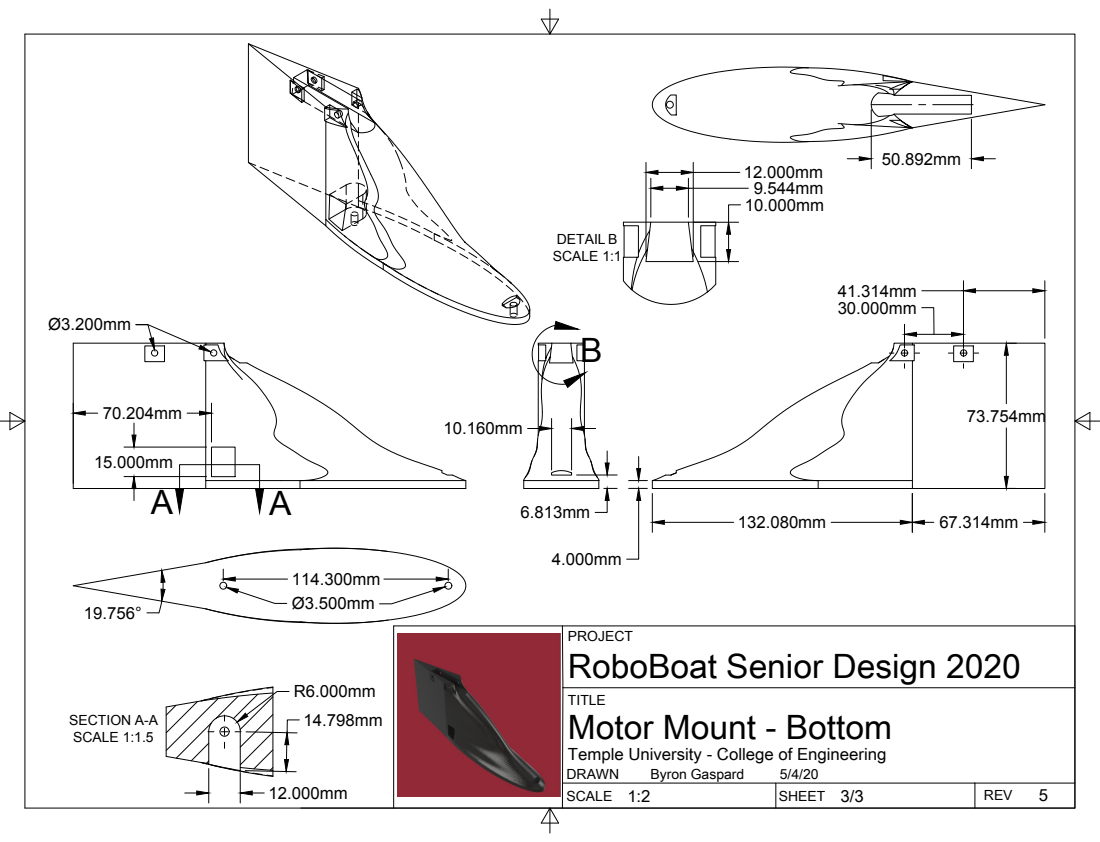
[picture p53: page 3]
SCALE 1:2; SHEET 3/3; REV; Byron Gaspard; SECTION A-A SCALE 1:1.5; DETAIL B SCALE 1:1

PROJECT
RoboBoat Senior Design 2020

TITLE
Motor Mount - Bottom

Temple University - College of Engineering
DRAWN

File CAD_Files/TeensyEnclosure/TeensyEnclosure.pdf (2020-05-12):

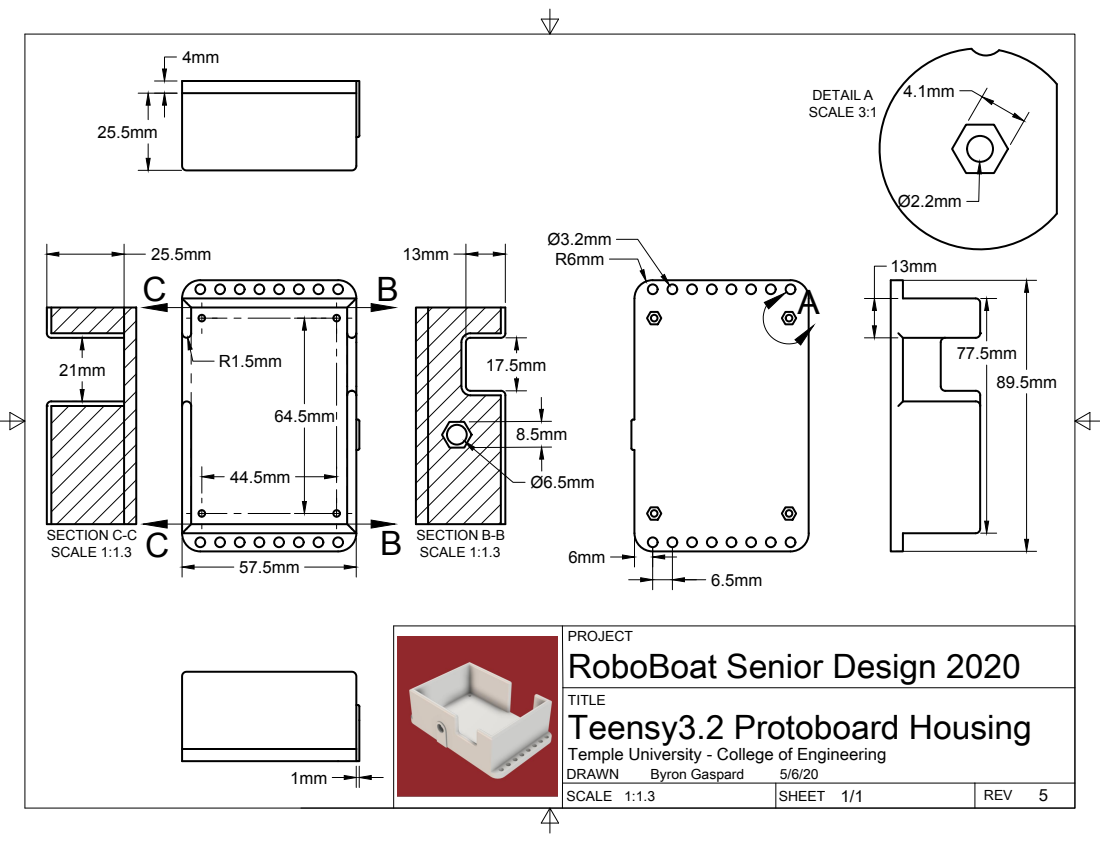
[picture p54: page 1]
SCALE 1:1.3; SHEET 1/1; REV; Byron Gaspard; Teensy3.2 Protoboard Housing; DETAIL A SCALE 3:1; SECTION B-B C; SECTION C-C SCALE 1:1.3

PROJECT
RoboBoat Senior Design 2020

Temple University - College of Engineering
DRAWN

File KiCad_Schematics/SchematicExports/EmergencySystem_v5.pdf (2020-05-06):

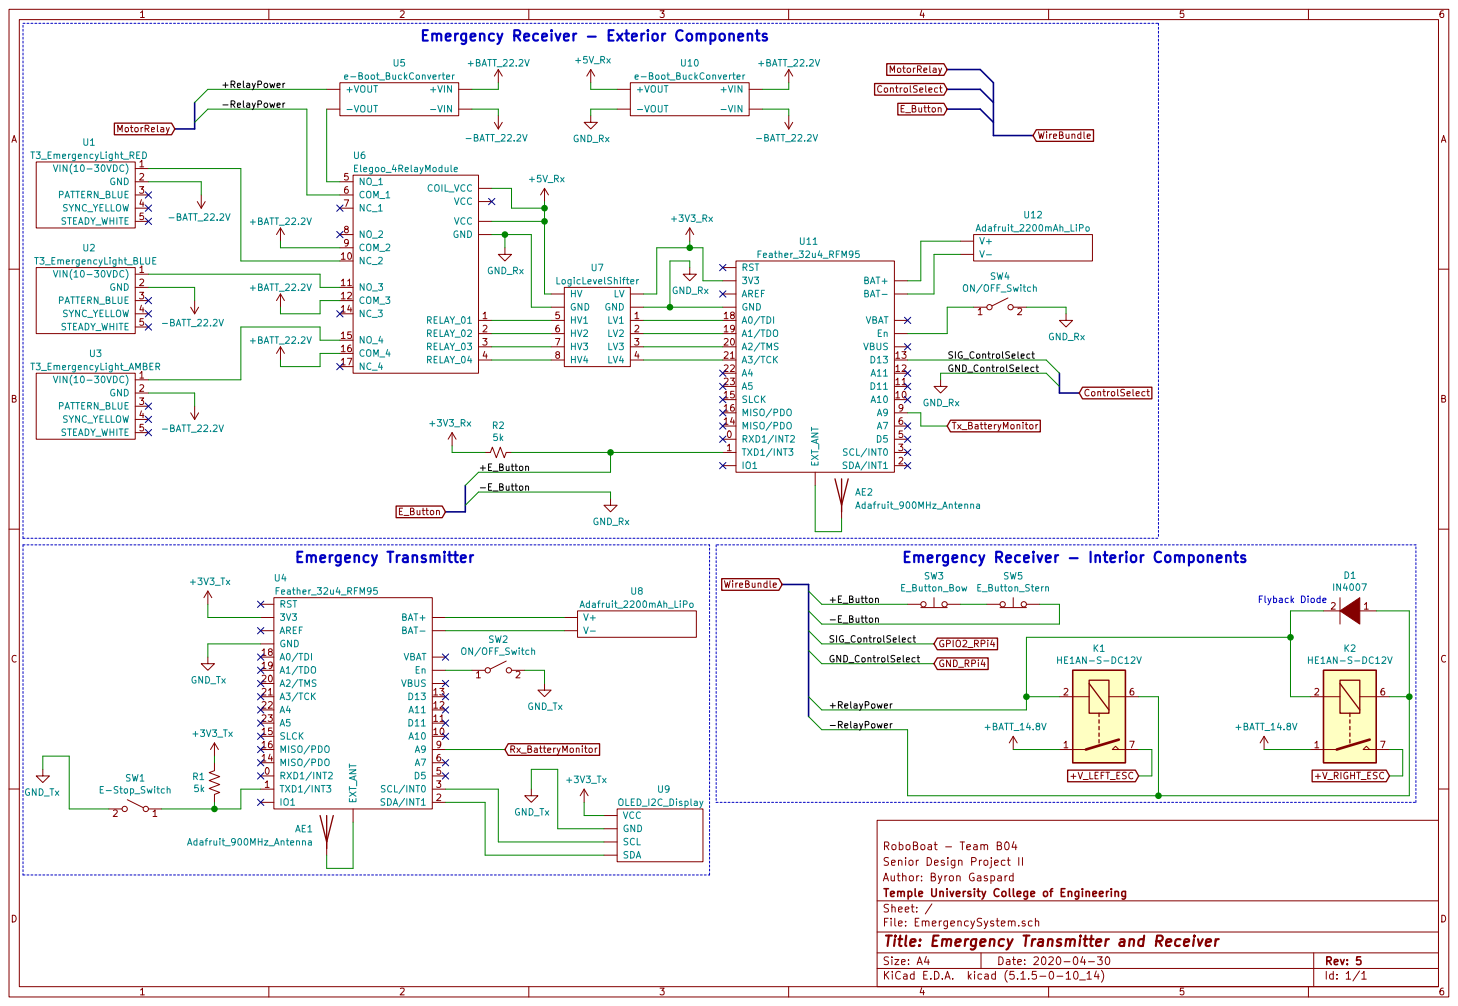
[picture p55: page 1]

Emergency Receiver - Exterior Components

Emergency Receiver - Interior Components

Author: Byron Gaspard
File: EmergencySystem.sch Sheet: / Temple University College of Engineering

Id: 1/1 Title: Emergency Transmitter and Receiver

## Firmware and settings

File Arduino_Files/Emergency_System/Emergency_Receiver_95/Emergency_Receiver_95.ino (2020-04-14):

#include <Adafruit_SleepyDog.h> // Adds watchdog timer that will reset the transmitter if it stops for 10 seconds
#include <RH_RF95.h>
#include <SPI.h>
#include <string.h>
#include <stdio.h>
#include <math.h>

// ~~~~~~~~~~~~~~~~~~~~~~~~~~~~~~~~~~~~~~~~~~~~ Watchdog Setup ~~~~~~~~~~~~~~~~~~~~~~~~~~~~~~~~~~~~~~~~~~
#define WATCHDOG_TIMEOUT 10000 // Time of inactivity before restarting the arduino

// ~~~~~~~~~~~~~~~~~~~~~~~~~~~~~~~~~~~~~~~~~~~~~~ Radio Setup ~~~~~~~~~~~~~~~~~~~~~~~~~~~~~~~~~~~~~~~~~~~
#define RFM95_RST 4 // The reset pin for the radio
#define RFM95_INT 7 // Slave select pin for the radio
#define RFM95_CS 8  // Chip select pin for the radio

#define RF95_FREQ 915.0   // Operating frequency of emergency receiver

RH_RF95 rf95(RFM95_CS, RFM95_INT); // Singleton instance of the radio driver

#define SIZE_radiopacket 50 // Max size of transmission
uint8_t buf[SIZE_radiopacket]; // Input buffer for the radio - declared globally to keep out of the stack
uint8_t len; // Holds the actual size of th received message

// The duration of time that the radio will wait to receive a packet
#define RF_TIMEOUT_MS     1000

// The number of consequitive dropped packets that signify a disconnect event
#define RF_DROP_PACKET_DISCONNECT   3

volatile unsigned int missCnt = 0; // Holds the current count of consequitive failed transmissions

char okMsg[] = "TempleBoatNormal"; // Message that indicates a non-emergency state sent by the transmitter
char batReading[20]; // Holds the battery Reading
char rssiReading[20]; // Holds the RSSI
char switchReading[20]; // Holds the switch Value

// Holds the current status of the emergency state as determined by the remote kill-switch
volatile byte EmergencyState_RF = true;

int ii;

// ~~~~~~~~~~~~~~~~~~~~~~~~~~~~~~~~~~~~~~~~~~~ E-Switch Setup ~~~~~~~~~~~~~~~~~~~~~~~~~~~~~~~~~~~~~~~~~~~
// This pin is the pin that the physical emergency switches are connected to
#define PIN_EMERGENCY_SWITCH  1
/* if HIGH -> Emergency State
   if LOW -> Normal State (Manual or Autonomous)  */

// Holds the current status of the emergency state as determined by the onboard kill-switches
volatile byte EmergencyState_SW = true;

// ~~~~~~~~~~~~~~~~~~~~~~~~~~~~~~~~~~~~~~~~~~~~~~ Relay Setup ~~~~~~~~~~~~~~~~~~~~~~~~~~~~~~~~~~~~~~~~~~~

// Calculates the net emergency state given radio and button state
#define EMERGENCY_STATE   EmergencyState_SW || EmergencyState_RF
//volatile byte EmergencyState = true;

// These are the pins that the relay control signals are connected to
#define PIN_MOTOR_RELAY       18
#define PIN_AMBER_LIGHT       19
#define PIN_RED_LIGHT         20
#define PIN_BLUE_LIGHT        21

// These are the values to turn ON the corresponding relay devices
#define ON_MOTOR              LOW
#define ON_RED                HIGH
#define ON_BLUE               LOW
#define ON_AMBER              LOW

// ~~~~~~~~~~~~~~~~~~~~~~~~~~~~~~~~~~~~~~~~~~~~~~ State Select Setup ~~~~~~~~~~~~~~~~~~~~~~~~~~~~~~~~~~~~
// This is the pin that is connected to the Raspberry Pi 4 that determines indicated if we are in the
// manual control or autonomous control state so the lights can be selected accordingly
#define PIN_CONTROL_SELECT    13
// if HIGH -> Manual Control (AMBER)
// if LOW -> Automous Control (BLUE)

// ======================================Battery Monitor Setup=====================================================
#define VBATPIN A9  // The analog pin connected to the battery
#define CHRG_V 4.2  // The changed voltage of the batter
#define EMPT_V 3.0  // The discharged voltage of the battery
float measuredvbat;
unsigned char percent;

void setup()
{
  // ~~~~~~~~~~~~~~~~~~~~~~~~~~~~~~~~~~~~~~~ Digital I/O Configuration ~~~~~~~~~~~~~~~~~~~~~~~~~~~~~~~~~~~~
  // configure the pin that congrols the main motor relays to output
  pinMode(PIN_MOTOR_RELAY, OUTPUT);

  // Configure the pin that controls the LEDs to output
  pinMode(PIN_RED_LIGHT, OUTPUT);
  pinMode(PIN_BLUE_LIGHT, OUTPUT);
  pinMode(PIN_AMBER_LIGHT, OUTPUT);

  // Configure the pin that controls the manual/autonomous select to input
  pinMode(PIN_CONTROL_SELECT, INPUT_PULLUP); // Use the internal pullup resistor

  // Configure the pin that will be connected to the onboard kill-switches to be input
  pinMode(PIN_EMERGENCY_SWITCH, INPUT); // Pullup resistor soldered onto the board

  stateHandler(); // Call the state handler to put the system into the emergency state from the start

  // Read the value of the onboard kill-switch pin
  EmergencyState_SW = digitalRead(PIN_EMERGENCY_SWITCH);

  // Configure the pin-change interrupt handler for the onboard kill-switches
  //  attachInterrupt(digitalPinToInterrupt(PIN_EMERGENCY_SWITCH), ISR_EmergencyStateChange, CHANGE);

  // ~~~~~~~~~~~~~~~~~~~~~~~~~~~~~~~~~~~~~~~ Serial Monitor Configuration ~~~~~~~~~~~~~~~~~~~~~~~~~~~~~~~~~
  //Serial.begin(9600);

  // ~~~~~~~~~~~~~~~~~~~~~~~~~~~~~~~~~~~~~~~~~~~~~ Radio Configuration ~~~~~~~~~~~~~~~~~~~~~~~~~~~~~~~~~~~
  // Manual reset of the radio
  pinMode(RFM95_RST, OUTPUT);
  digitalWrite(RFM95_RST, HIGH); delay(100);
  digitalWrite(RFM95_RST, LOW);  delay(10);
  digitalWrite(RFM95_RST, HIGH); delay(10);

  // Initialize radio and ensure that it is successful
  while (!rf95.init()) ; // Serial.println("LoRa radio init failed");
  //Serial.println("LoRa radio init OK!");

  // Set frequency and ensure that it is successful
  if (!rf95.setFrequency(RF95_FREQ)) ; //Serial.println("setFrequency failed");
  //else Serial.print("Set Freq to: "); Serial.println(RF95_FREQ);
  // Set the transmit power of the radio
  rf95.setTxPower(23, false);

  // Used for testing. Ensures that reset from watchdog timer is captured on the transmitter
  // Remove for production & actual use to ensure quick reset in the case of a run-time error that forces reset
  delay(5000);

  // ~~~~~~~~~~~~~~~~~~~~~~~~~~~~~~~~~~~~~~~~~~ Watchdog Reset Timer ~~~~~~~~~~~~~~~~~~~~~~~~~~~~~~~~~~~~~~
  Watchdog.enable(WATCHDOG_TIMEOUT); // Enable the watchdog timer

}

// =====================================================================================================
void loop()
{
  stateHandler();
  radio_Update();

  if (missCnt >= RF_DROP_PACKET_DISCONNECT)  // If three packets are missed in a row, we are now in the emergency state
    EmergencyState_RF = true;

  Watchdog.reset(); // Reset the watchdog timer
  // If the line of code above isn't encountered every 10 seconds, the arduino will reset

}

// ====================================================================================================
void stateHandler() {
  EmergencyState_SW = digitalRead(PIN_EMERGENCY_SWITCH);
  if (EMERGENCY_STATE) {    // Will be executed if we are in emergency state
    digitalWrite(PIN_MOTOR_RELAY, !ON_MOTOR);
    digitalWrite(PIN_RED_LIGHT, ON_RED);
    digitalWrite(PIN_BLUE_LIGHT, !ON_BLUE);
    digitalWrite(PIN_AMBER_LIGHT, !ON_AMBER);
  }
  else {    // Will be executed if we are NOT in the emergency state
    digitalWrite(PIN_MOTOR_RELAY, ON_MOTOR);
    digitalWrite(PIN_RED_LIGHT, !ON_RED);

    if (digitalRead(PIN_CONTROL_SELECT) == HIGH) {    // If in manual control mode
      digitalWrite(PIN_BLUE_LIGHT, ON_BLUE);
      digitalWrite(PIN_AMBER_LIGHT, !ON_AMBER);
    }
    else {    // If in autonomous control mode
      digitalWrite(PIN_BLUE_LIGHT, !ON_BLUE);
      digitalWrite(PIN_AMBER_LIGHT, ON_AMBER);
    }
  }
}

// =====================================================================================================
void radio_Update() { // This function will respond to the transmitter and send additional information

  len = sizeof(buf);
  if (rf95.waitAvailableTimeout(RF_TIMEOUT_MS)) { //Wait for 1 second for the receiver to respond
    if (rf95.recv(buf, &len)) { // Should be a reply message for us now
      if ((strlen(buf)) == strlen(okMsg)) {
        missCnt = 0; // Reset missCnt as we just had a successful handoff
        //Serial.print("strlen(buf): "); Serial.println(strlen(buf));
        //Serial.print("okMsg: "); Serial.println(strlen(okMsg));
        // Compare the recieved and the known "OK" string
        for (ii = 0; (okMsg[ii] == (char)buf[ii] && ((char)buf[ii] != '\0')); ii++);

        // The emergency state is set if the received string does not match the OK string
        if ( ( ( (char)buf[ii] == '\0' ) && ( okMsg[ii] == '\0' ) ) ) // This is TRUE during normal operation
          EmergencyState_RF = false; // Set EmergencyState_RF to FALSE if the recived message indicates normal operation
        else // Set EmergencyState_RF to TRUE if the recived message indicates emergency operation
          EmergencyState_RF = true;

        stateHandler();
        // Gather and convert battery, RSSI, and switch value into strings
        itoa(measureBattery(), batReading, 10);
        itoa(rf95.lastRssi(), rssiReading, 10);
        if (EmergencyState_SW) itoa(1, switchReading, 10);
        else itoa(0, switchReading, 10);

        // Add the battery, RSSI, and switch value to the buffer for the response
        strcat(buf, " ");
        strcat(buf, batReading);
        strcat(buf, " ");
        strcat(buf, rssiReading);
        strcat(buf, " ");
        strcat(buf, switchReading);

        //Serial.print("Sending: "); Serial.println((char*)buf);


        rf95.send((uint8_t *)buf, sizeof(buf));    // Send a response to the transmitter
        rf95.waitPacketSent();  // Wait until the packet has been sent before continuing
      }
      else {
        missCnt++;
        //Serial.println("Invalid length");
      }
    }
    else { // if receive fails
      missCnt++;
      //Serial.println("Receive failed");
    }
  }
  else { // Encountered if we wait and still fail to receive a response from reciever
    missCnt++;
    //Serial.println("No reply, is there a listener around?");
  }
}

// =========================================Baterry Measurement=========================================
unsigned char measureBattery() {
  measuredvbat = analogRead(VBATPIN);
  measuredvbat *= 2;    // we divided by 2, so multiply back
  measuredvbat *= 3.3;  // Multiply by 3.3V, our reference voltage
  measuredvbat /= 1024; // convert to voltage
  percent = 100 * ((measuredvbat - EMPT_V) / (CHRG_V - EMPT_V));
  if (percent > 100) percent = 100;
  return percent;
}

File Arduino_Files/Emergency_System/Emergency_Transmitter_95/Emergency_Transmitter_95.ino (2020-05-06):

#include <Adafruit_SleepyDog.h> // reset the transmitter if it stops for 10 seconds
#include <Adafruit_SSD1306.h> // Adds OLED display support 
#include <Wire.h> // Adds I2C Oled Support
#include <RH_RF95.h> // Adds support for the LoRa Radio

// ~~~~~~~~~~~~~~~~~~~~~~~~~~~~~~~~~~~~~~~~~~~~ Watchdog Setup ~~~~~~~~~~~~~~~~~~~~~~~~~~~~~~~~~~~~~~~~~~
#define WATCHDOG_TIMEOUT 10000 // Time of inactivity before restarting the arduino

// ~~~~~~~~~~~~~~~~~~~~~~~~~~~~~~~~~~~~~~~~~~~~ OLED Display Setup ~~~~~~~~~~~~~~~~~~~~~~~~~~~~~~~~~~~~~~
#define SCREEN_WIDTH 128 // OLED display width, in pixels
#define SCREEN_HEIGHT 64 // OLED display height, in pixels

#define OLED_RESET -1   // Reset pin # (sharing Arduino reset pin as it is -1)

// Declaration for an SSD1306 display connected to I2C (SDA, SCL pins)
Adafruit_SSD1306 display(SCREEN_WIDTH, SCREEN_HEIGHT, &Wire, OLED_RESET);

unsigned char displayInitSuccess = 0;

// ~~~~~~~~~~~~~~~~~~~~~~~~~~~~~~~~~~~~~~~~~~~ E-Switch Setup ~~~~~~~~~~~~~~~~~~~~~~~~~~~~~~~~~~~~~~~~~~~
#define PIN_EMERGENCY_SWITCH 1 // The pin that the emergency switch is connected to
unsigned char Tx_E_Switch;

// ~~~~~~~~~~~~~~~~~~~~~~~~~~~~~~~~~~~~~~~~~~~~~~ Radio Setup ~~~~~~~~~~~~~~~~~~~~~~~~~~~~~~~~~~~~~~~~~~~
#define RFM95_RST 4 // The reset pin for the radio
#define RFM95_INT 7 // Slave select pin for the radio
#define RFM95_CS 8  // Chip select pin for the radio

#define RF95_FREQ 915.0   // Operating frequency of emergency receiver
RH_RF95 rf95(RFM95_CS, RFM95_INT); // Singleton instance of the radio driver

#define RF_DROP_PACKET_DISCONNECT   3 // Number of dropped paxkets that results in a disconnect event
#define RF_TIMEOUT_MS     1000 // How long we should wait for a response before retransmitting

#define SIZE_radiopacket 50 // Max size of transmission

uint8_t buf[SIZE_radiopacket];  // Input buffer for the radio - declared globally to keep out of the stack
uint8_t len; // Holds the actual size of th received message

char *strtok_prt; // Used to tokinize message from the receiver to extract relevant information
unsigned char RxBattery = 0;  // Holds the receiver's battery percentage
unsigned char Rx_E_Switch = 0; // Holds the receiver's emergency switch state

int16_t RxRssi = 2; // Holds the receiver's TxRssi
int16_t TxRssi = 2; // Holds the transmitters TxRssi

volatile unsigned int successMsgs = 0; // Holds the total number of successfuly transmissions
volatile unsigned int failMsgs = 0; // Holds the total number of failed tramsissions

volatile unsigned int missCnt = 0; // Holds the current count of consequitive failed transmissions
volatile unsigned int discCnt = 0;  // Holds the number of disconnect events since power-up

// ~~~~~~~~~~~~~~~~~~~~~~~~~~~~~~~~~~~~~~~~~ Battery Monitor Setup ~~~~~~~~~~~~~~~~~~~~~~~~~~~~~~~~~~~~~~
#define VBATPIN A9  // The analog pin connected to the battery
#define CHRG_V 4.2  // The changed voltage of the batter
#define EMPT_V 3.0  // The discharged voltage of the battery

float measuredvbat;
unsigned char percent;

// =====================================================================================================
void setup() {
  // ~~~~~~~~~~~~~~~~~~~~~~~~~~~~~~~~~~~~~~~ Serial Monitor Configuration ~~~~~~~~~~~~~~~~~~~~~~~~~~~~~~~~~
  //Serial.begin(9600);

  // ~~~~~~~~~~~~~~~~~~~~~~~~~~~~~~~~~~~~~~~~~~ Display Configuration ~~~~~~~~~~~~~~~~~~~~~~~~~~~~~~~~~~~~~
  // Print the success or failure of the display initialization
  if (!display.begin(SSD1306_SWITCHCAPVCC, 0x3C)) {
    //Serial.println(F("SSD1306 allocation failed"));
  }
  else {
    //Serial.println(F("SSD1306 allocation succeeded"));
    displayInitSuccess = 1; // Allow the display to be printed to
    display.clearDisplay(); // Clear the display
    display.setTextSize(1);
    display.setTextColor(WHITE);
    display.println("SSD1306 allocated");
    display.display(); // Update the output on the display
    delay(250);
  }

  // ~~~~~~~~~~~~~~~~~~~~~~~~~~~~~~~~~~~~~~~~~~~~~ Radio Configuration ~~~~~~~~~~~~~~~~~~~~~~~~~~~~~~~~~~~
  // Manual reset of the radio
  pinMode(RFM95_RST, OUTPUT);
  digitalWrite(RFM95_RST, HIGH); delay(100);
  digitalWrite(RFM95_RST, LOW);  delay(10);
  digitalWrite(RFM95_RST, HIGH); delay(10);

  // Initialize radio and ensure that it is successful
  while (!rf95.init()) {
    //Serial.println("LoRa radio init failed");
    if(displayInitSuccess) display.println("LoRa init failed");
    if(displayInitSuccess) display.display();
  }
  //Serial.println("LoRa radio init OK!");
  if(displayInitSuccess) display.println("LoRa init OK!");
  if(displayInitSuccess) display.display();
  delay(250);

  // Set frequency and ensure that it is successful
  if (!rf95.setFrequency(RF95_FREQ)) {
    //Serial.println("setFrequency failed");
    if(displayInitSuccess) display.println("setFrequency failed");
    if(displayInitSuccess) display.display();
  } else {
    //Serial.print("Set Freq to: "); Serial.println(RF95_FREQ);
    if(displayInitSuccess) display.print("Set Freq to: "); display.println(RF95_FREQ);
    if(displayInitSuccess) display.display();
    delay(250);
  }
  // Set the transmit power of the radio
  rf95.setTxPower(23, false);

  // ~~~~~~~~~~~~~~~~~~~~~~~~~~~~~~~~~~~~~~~~~~ E-Switch Configuration ~~~~~~~~~~~~~~~~~~~~~~~~~~~~~~~~~~~~
  // Configure the pin that the switch is connected to to input - hardware pullup installed on board
  pinMode(PIN_EMERGENCY_SWITCH, INPUT);
  // Set the Tx_E_Switch variable to the state of the emergency switch's input pin
  Tx_E_Switch = digitalRead(PIN_EMERGENCY_SWITCH);

  // ~~~~~~~~~~~~~~~~~~~~~~~~~~~~~~~~~~~~~~~~~~ Watchdog Reset Timer ~~~~~~~~~~~~~~~~~~~~~~~~~~~~~~~~~~~~~~
  Watchdog.enable(WATCHDOG_TIMEOUT); // Enable the watchdog timer

  // ~~~~~~~~~~~~~~~~~~~~~~~~~~~~~~~~~~~~~~~~~~ Other ~~~~~~~~~~~~~~~~~~~~~~~~~~~~~~~~~~~~~~~~~~~~~~~~~~~~~
  // Clear the display and wait 2 seconds (this makes the arduino easier to re-program the arduino)
  if(displayInitSuccess) display.clearDisplay();
  if(displayInitSuccess) display.display();
  delay(2000);
}

// =====================================================================================================
void loop() {

  Tx_E_Switch = digitalRead(PIN_EMERGENCY_SWITCH); // Update the switch value

  radio_Update(); // Try to talk to the receiver

  // Disconnect event occurs after three missed transmissions
  if (missCnt == RF_DROP_PACKET_DISCONNECT) {
    discCnt++;
  }

  if(displayInitSuccess) updateDisplay(); // Update the output on the display

  Watchdog.reset(); // Reset the watchdog timer
  // If the line of code above isn't encountered every 10 seconds, the arduino will reset
}
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

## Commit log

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2020-01-16 changed file name to allow it to be opened by the arduino IDE
2020-01-16 updated teensy motor pin PWM ooutputs and edited the start script to run on ubuntu server
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2020-01-21 Updated the teensyMotorControl.ino file to also read data from the BNO055 sensor and publish it with ROS Serial Arduino. The start boat shell script was also updated to reflect the new gnome-terminal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
2020-01-21 Added schematic for the teensy3.2 motor controller and IMU sensor input
    [Adafruit BNO055.brd, Adafruit BNO055.sch, AdafruitBNO055.sch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]
2020-01-22 Updated bugs with KiCad Libraries
    [TeensySchematic.kicad_pcb, TeensySchematic.sch]
2020-01-22 removing deleted files from tracking
    [Adafruit BNO055.brd, Adafruit BNO055.sch, AdafruitBNO055.sch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]
2020-01-22 Created Schematic for Emergency Receiver
    [EmergencySystem.kicad_pcb, EmergencySystem.sch]
2020-01-23 Finalized the initial version of the emergency transmitter/receiver schematic. PDF export was also uploaded.
    [EmergencySystem.sch]
2020-01-23 Fixed symbol naming issues
    [EmergencySystem.sch]
2020-01-24 Added Ultimate GPS to the Teensy Schematic and updated our custom symbol library
    [EmergencySystem.sch, TeensySchematic.sch]
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2020-01-26 updated motor control schematic to include GPS
    [TeensySchematic.sch]
2020-01-26 Renamed battery mnonitor file so that it could be opened in arduino IDE
2020-01-26 Added libraries required for using the radio and ultimate GPS from Adafruit in case they go missing in the future
2020-01-27 Create ZED Installation Error on Jetson TX2
    Could not open zed tools or run zed-ros-wrapper display_zed.launch. This resolved the problem. However, ZED firmware needs to be updated.
2020-01-28 Fixed incorrect hardware serial wiring in the schematic
    [TeensySchematic.sch]
2020-01-28 Updated to killBoat shell script to fix errors and integrated the GPS into the teensy motor board
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2020-01-30 adding battery monitor schematic
    [Schematic.kicad_pcb, Schematic.sch]
2020-01-31 Updated battery monitor schematic, simulation results and added a PDF files of all the updated schematics
    [ADC_Input_Simulation_Results.xlsx, BatteryMonitor.kicad_pcb, BatteryMonitor.sch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]
2020-02-04 Created an initial power distribution schematic
    [PowerDistribution.kicad_pcb, PowerDistribution.sch]
2020-02-04 Add files via upload
    Relay and LED test (0v0)
    can't react immediately after changing E-stop button to interrupt pin (>x<)
    possible issue: button connection not tight? receiver code?
    [Emergency_Receiver_95.ino]
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2020-02-04 Add files via upload
    Move the E-stop button from pin12 to pin0(interrupt pin)
    Transmitter reacts faster (OvO)
    Receiver not always reacts or reacts delay (TxT)
2020-02-05 Add files via upload
    Cutoff circuit if lost connection with transmitter for 5 sec (OvO)
    >>: Cut if low battery (TxT)
2020-02-05 Add files via upload
    The switch detection is still unstable but better after changing jump wires (=皿=#)
    >>: Shorter the delays on sending and printing word
    [Emergency_Transmitter_95.ino]
2020-02-06 Add files via upload
    Should be able to send a message when Rx battery is lower than 10%, not tested yet
2020-02-06 Add files via upload
    OLED screen shows the message received from Rx
    >>: OLED screen shows "Disconnected" mistakenly ToT
    [Emergency_Transmitter_95.ino]
2020-02-07 Update Emergency_Transmitter_95.ino
    Transmitter circuit done *>V<*
    E-stop button changes to pin 1 instead of pin 0
    >>: fix the long react time
    [Emergency_Transmitter_95.ino]
2020-02-07 Updated KiCad Schematics
    [EmergencySystem.sch, PowerDistribution.sch]
2020-02-07 added solidworks motor mount models
    [Left part2.SLDPRT, Part 1_new.SLDPRT, Right part2.SLDPRT]
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2020-02-14 updated schematcs and images for presentation
    [ADC_Input_Simulation_Results.xlsx, EmergencySystem.sch, SimulatedBatteryVoltage_NoVoltageDivider.csv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]
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2020-02-22 Updated the power distribution schematic
    [PowerDistribution.sch]
2020-02-24 Revert "Emergency Transmitter"
    This reverts commit 6d25a2bf25d5367a99fc9839bb3c3e94ecd05ad8.
    [Emergency_Transmitter_95.ino]
2020-02-24 Revert "EmergencyReceiver"
    This reverts commit fdb66eed55c9dec7330918a58b9510bfca4de544.
    [Emergency_Receiver_95.ino]
2020-02-27 Commented code and modified to work with actual wiring in the emergency receiver
2020-02-29 Added backup configuration files for the boat's three wireless routers to allow them to be easily restored in the event of a misconfiguration
2020-02-29 Reorganized and renamed files
    [ADC_Input_Simulation_Results.xlsx, BatteryMonitor.kicad_pcb, BatteryMonitor.sch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]
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2020-03-10 Updated the kicad schatic to include the logic-level shifter. Also modified the layout to indicate the emergency receiver components that are on the inside/outside of the boat
    [EmergencySystem.sch]
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2020-03-13 Updated router backs and firmware filez
    [5537T502_ALUMINUM T-SLOTTED FRAMING EXTRUSION.SLDPRT, TSlotFlatMount.stl]
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2020-03-18 Added images and CAD files
    [5537T502_ALUMINUM T-SLOTTED FRAMING EXTRUSION.SLDPRT, Left part2.SLDPRT, Lidar Base(2_above).SLDASM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]
2020-03-19 Added images of the hardware
    [5537T502_ALUMINUM T-SLOTTED FRAMING EXTRUSION.SLDPRT, Arduino_Mega_Mounting_Plate.stl, Left part2.SLDPRT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]
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2020-03-20 Updated battery monitor code withthe new calibration scale values obtained from testing inputs at 6 different voltages
2020-03-28 Added the updated CAD files
    [ByronRevisions.stl, CE3_LidarEnclosure_Base.3mf, CE3_LidarEnclosure_Lid.3mf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]
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2020-03-31 Added shell scripts for starting the ZED camera and video stretaming service
2020-04-01 Adding ROS functionlaity to battery monitor, created shell scripts to launch both ZED camera and web server
2020-04-04 Updated the website and the arduino code. The website now streams IMU data in real-time. Additionally, the GPS location data is plotted on a map
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2020-04-14 Updating emergency transmitter code and CAD files
    [CE3_MotorMountTop_Final.3mf, CE3_MotorMount_BottomFinal.3mf, CE3_MotorMount_Top_Final.3mf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]
2020-04-23 Updated images and schematics
    [EmergencySystem.sch]
2020-04-23 updated schematics
    [EmergencySystem.sch, PowerDistribution.sch, TeensySchematic.sch]
2020-04-25 Update Battery_Monitor.ino
    Fixed Scaling Value
    [Battery_Monitor.ino]
2020-05-06 Updates to images, schematics, and arduino code
    [BatteryMonitor.sch, EmergencySystem.sch, PowerDistribution.sch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]
2020-05-12 Updated CAD models and networking guides
    [5537T502_ALUMINUM T-SLOTTED FRAMING EXTRUSION.SLDPRT, Arduino_Mega_Mounting_Plate.stl, ByronRevisions.stl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]
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2020-05-19 Updated boat website to add LIDAR scan data and information on the scan messages. Created tables to make controls/states more readable
    [Chest.obj, FireHydrantMesh.obj, Utah_teapot_(solid).stl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]
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2020-09-04 Update index.html
    A change in the HTML5 Gamepad API cause the index of the start button to change. Updated to the new and correct mapping.
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
